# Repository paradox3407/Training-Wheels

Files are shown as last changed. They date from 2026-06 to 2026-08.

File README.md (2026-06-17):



# Training Wheels

ESP32 based two wheeled self balancing robot with a custom PCB, chassis, firmware! Want to learn how to implement a control loop or just want to build a cool robot? Training Wheels is for you! 

## Features

- PID Control Algorithm 
- IMU Calibration Program
- Convenient Troubleshooting:
  - Headers for swapping ICs: ESP32, MPU6050, A4988 Stepper Motor Driver Breakout
  - LED indicators for VDD and GPIO 
- Nema 17 Stepper Motors
- Power Switch

## Overview

This project was made for [Hackclub's](https://hackclub.com/programs) Fallout Program. I built this because I wanted to make a project that encompasses mechanical, electrical, and software engineering, all while exploring PID control through implementing the prototyping process and good design practices. Through the ~70 hours spent on this project I learned the value of documentation, time management, how to select components, read datasheets, how to CAD using assemblies and designing in context, schematic, part layout and wiring good practices, version control, PID control theory and tuning, and so much more! (Might have gotten a caffeine addiction too...)

## Gallery 

<details>
  <summary> Click to expand </summary>
  <br>

  ### Chassis / Assembly
  *Designed in Onshape* 
  
  Source Files found [here](https://cad.onshape.com/documents/563a6cb8d162cb6cd823a1f9/w/2660c435afac39828b2200f7/e/e81ee193bff4145dfd9a22a6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)

  <p align="center">
    
    
  </p>

  ### PCB 
  *Designed in KiCad*

  <p align="center">
    
  </p>

  #### Schematic
  Schematic

  #### Layout
  PCB Layout

</details>

## Firmware (Setup + Tuning)

*Written in C++ using VSCode + [PlatformIO](https://platformio.org/)*

### How to Build & Flash
1. Clone this repository.
2. Open the `Firmware/Self-Balancing-Robot` folder in VS Code with PlatformIO installed.
3. Connect your ESP32 via USB.
4. Click the PlatformIO **Upload** button 

The IMU must be calibrated before running the main code. Run the [calibration program](./Firmware/Self-Balancing-Robot/src/calibration/MPU_calibration.cpp) while the robot is upright and in a stable position. 

### How to Tune

Then run the [main code](./Firmware/Self-Balancing-Robot/src/robot_main/main.cpp). To get the robot to balance, modify these values:

```cpp
const float desiredOutput = 0; // desired angle 
const float Kp = 0; 
const float Ki = 0;
const float Kd = 0; 
```
Tune these values in the following order: 
`desiredOutput` is used for setting the offset for the balance point of the robot. 

`Kp` is the proportional gain, and it will be doing most of the "work": increase by powers of two until the robot oscillates, then decrease by 20%.

`Kd` is the derivative gain, and it addresses oscillations. Increase by small increments, starting roughly at 0.05, until the robot stops oscillating. 

`Ki` is the integral gain, which address drift. By this point the robot should be balancing but if it glides forward or backwards, increase this value, also starting small. Note that `Ki` might not always need to be modified. 

The key to tuning is patience! Only modify one value at a time, and increment in small values. 

## Zine

*Designed in Figma*

Training Wheels Zine-Final-1

## Acknowledgements

Designed by Sara C / paradox3407

**Special thanks** to my robotics mentors for reviewing my designs and giving me much needed feedback! + Jennifer for creating inspiration/reference sketches for the chassis + Ellie for teaching me the basics of calculus at flex when I was trying to learn the math behind PID + Hackclub and Fallout!

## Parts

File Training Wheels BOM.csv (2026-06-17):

Item | Description | Quantity | Unit Price ($) | Total Price ($) | URL | Running Total ($ with Tax)
Pololu_Breakout_A4988 | Motor Driver | 2 | 8.95 | 17.9 | https://www.pololu.com/product/1182 | 19.2
ECA1HM101 | Capacitor | 2 | $0.45 | $0.90 | https://www.digikey.com/en/products/detail/panasonic-industry/ECA-1HM101/245041 | $20.75
Red SMD LED | Indicator LEDs | 2 | $0.15 | $0.30 | https://www.sparkfun.com/red-led-surface-mount-1206.html | $21.27
Screw_Terminal_01x02 | Power Terminal | 1 | $1.54 | $1.54 | https://www.mouser.com/ProductDetail/Altech/MV-152?qs=sGAEpiMZZMvPvGwLNS6715fLxDSS7ZPWguTwbRPpKV4%3D | $23.93
Wire Ferrules | For Power wires | 1 | 13.18 | 13.18 | https://www.aliexpress.com/i/2251832854626098.html?gatewayAdapt=4itemAdapt | $46.67
Stepper_Motor_bipolar | Motors | 2 | $9.13 | $18.26 | https://www.omc-stepperonline.com/nema-17-bipolar-45ncm-63-74oz-in-1-5a-42x42x39mm-4-wires-w-1m-pin-connector-17hs15-1504s-x1 | $55.43
GY-521 | MPU Breakout Board | 1 | $5.94 | $5.94 | https://www.aliexpress.us/item/3256809115197759.html?src=google&gatewayAdapt=glo2usa | $65.68
620 Ohm Resistor | Resistor | 1 | 0.1 | 0.1 | https://www.mouser.com/ProductDetail/YAGEO/AC1206FR-7W620RL | $65.85
270 Ohm Resistor | Resistor | 1 | $0.19 | $0.19 | https://www.mouser.com/ProductDetail/Vishay/RCA1206270RJNEA?qs=sGAEpiMZZMtlubZbdhIBIOxU6kuYwPD0YBDy2BQIpik%3D | $66.18
DEVKIT_V1_ESP32-WROOM-32 TYPE-C 30PIN | Microcontroller | 1 | $12.24 | $12.24 | https://www.aliexpress.us/item/3256809051361454.html?src=google&gatewayAdapt=glo2usa | $87.29
TSR_1-2450 | DC DC CONVERTER 5V 5W | 1 | $6.16 | $6.16 | https://www.digikey.com/en/products/detail/traco-power/TSR-1-2450/9383780 | $97.92
Bismuth Solder Paste | For SMD Soldering | 1 | 16.99 | 16.99 | https://www.amazon.com/Solder-Paste-Soldering-Electronic-Remove/dp/B0BVKB9PY4 | $127.23
LED Rocker Swith | Power Switch | 1 | $5.73 | $5.73 | https://www.aliexpress.us/item/3256810220221486.html?curPageLogUid=jQC0xfIuNxaA | $137.11
18650 2500mAh 20A Battery | Battery | 3 | $4.99 | $14.97 | https://www.18650batterystore.com/products/samsung-25r-18650?adgroupid=43081474946 | $162.93
18650 Battery Holder | Battery Holder | 1 | $2.40 | $2.40 | https://www.digikey.com/en/products/detail/dfrobot/FIT0539/8549502 | $167.07
S4B-EH | Motor connector | 2 | $0.16 | $0.32 | https://www.digikey.com/en/products/detail/jst-sales-america-inc/S4B-EH/926535 | $167.62
2.54mm 0.1" 15-pin Female Header | ESP32 Header | 2 | $1.63 | $3.26 | https://www.electromaker.io/shop/product/254mm-01-15-pin-female-header | $173.24
WR-PHD 2.54 MM SOCKET HEADER; 8 | Motor Driver Header | 5 | $0.40 | $2.00 | https://www.digikey.com/en/products/detail/w-rth-elektronik/61300811821/17737805 | $176.69
M3-0.5x12 Class 12.9 Alloy Flat Socket Head Cap Screws | Battery Mounting Screws | 6 | 0.18 | 1.08 | https://boltsandnuts.com/products/m3-0-5x12-class-12-9-alloy-flat-socket-head-cap-screws-black-oxide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 | $178.55
M3 x 6mm Full Thread Socket Cap Head Screws | PCB mounting Screws | 11 | 0.26 | 2.86 | https://accu-components.com/us/metric-cap-head-screws/3817-SSCF-M3-6-A2 | $183.48
85mm Mecanum Wheel High Grip Rubber Tires | Wheel | 2 | 6.73 | 13.46 | https://www.aliexpress.us/item/3256804851566721.html?gatewayAdapt=glo2usa4itemAdapt | $206.70
6mm coupling | Wheel Coupling | 2 | 6.73 | 13.46 | https://www.aliexpress.us/item/3256804851566721.html?gatewayAdapt=glo2usa4itemAdapt | $229.92
PCB | PCB | 1 | $4.00 | $4.00 | https://cart.jlcpcb.com/quote | $236.82
 |  |  |  |  | Total: | $236.82

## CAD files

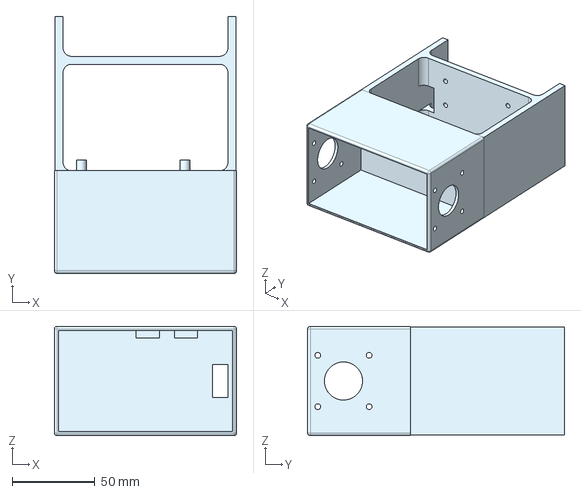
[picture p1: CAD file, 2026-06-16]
CAD Files/3D prints/Chassis V3 - Bottom.step
110.0 x 155.0 x 66.0 mm

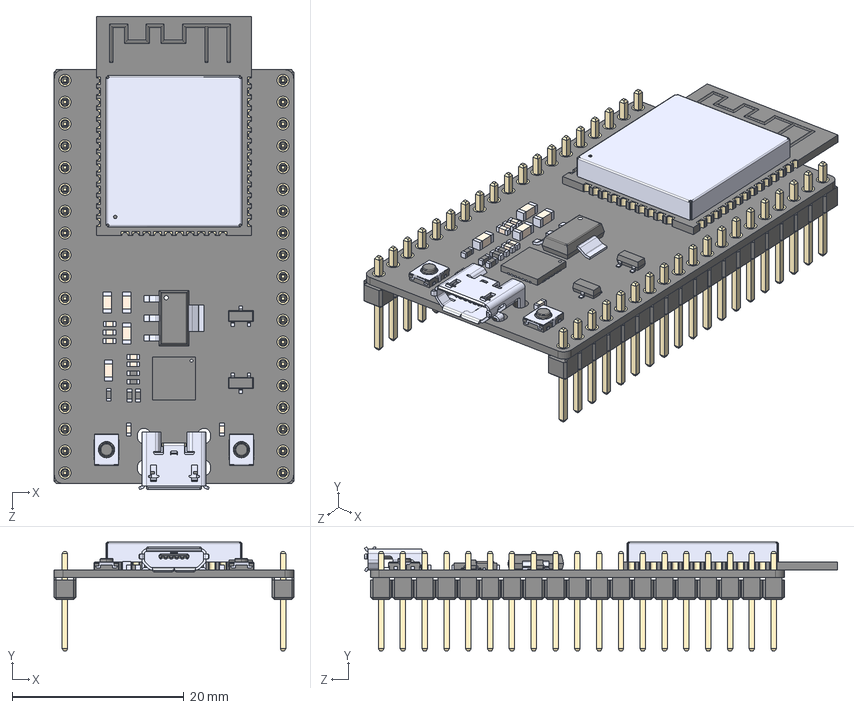
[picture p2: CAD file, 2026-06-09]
CAD Files/PCB Design/Kicad Tools/DEVKIT_V1_ESP32-WROOM-32/DEVKIT_V1_ESP32-WROOM-32.step
27.9 x 12.7 x 55.1 mm
board
header x 2
ESP32-WROOM-32D
micro usb
button x 2
CP2102N-A01-GQFN28
AMS1117-3.3
SS8050-G
components^DEVKIT V1 ESP32-WROOM-32

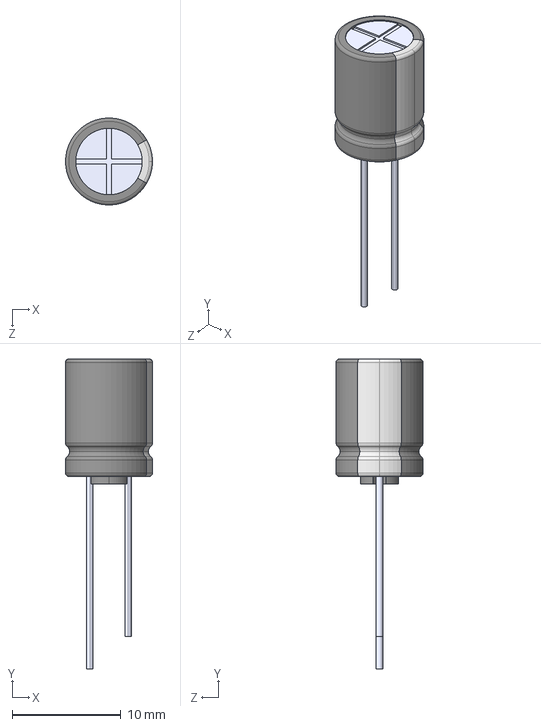
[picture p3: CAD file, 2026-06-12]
CAD Files/PCB Design/Kicad Tools/ECA1HM101/ECA1HM101.step
8.00 x 28.5 x 7.99 mm

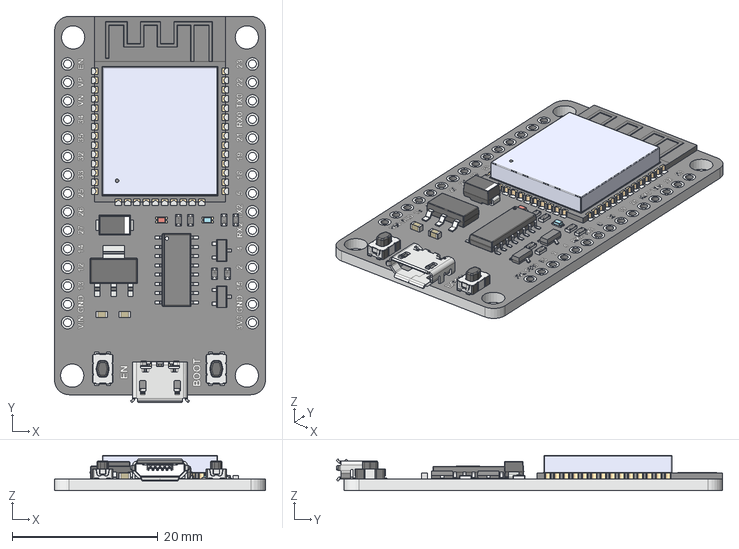
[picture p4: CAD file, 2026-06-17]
CAD Files/PCB Design/Kicad Tools/esp32_30pin-v3.step
29.0 x 53.1 x 4.86 mm

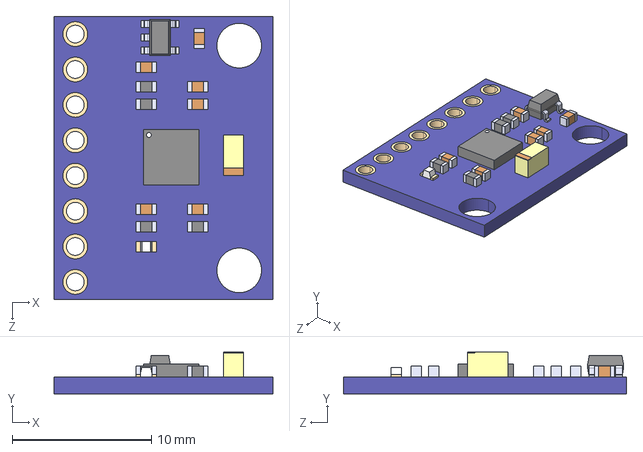
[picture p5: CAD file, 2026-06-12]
CAD Files/PCB Design/Kicad Tools/GY-521/GY-521.step
15.7 x 3.00 x 20.3 mm

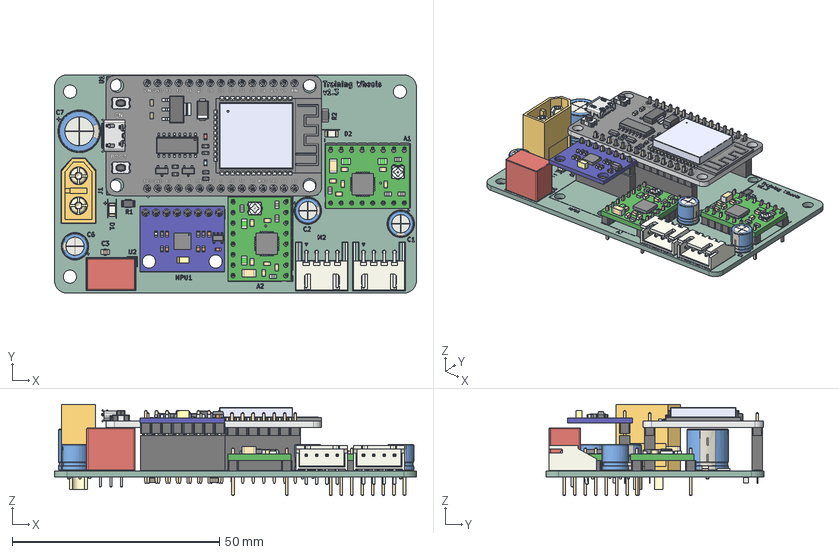
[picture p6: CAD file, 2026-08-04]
CAD Files/PCB Design/Self Balancing Robot/Self Balancing Robot.step
87.4 x 52.7 x 22.0 mm
R_1206_3216Metric x 2
CP_Radial_D6.3mm_P2.50mm x 3
GY-521
PinHeader_1x08_P2.54mm_Vertical x 5
PinSocket_1x08_P2.54mm_Vertical
MICRO USB B
PinSocket_1x15_P2.54mm_Vertical x 2
PinHeader_1x15_P2.54mm_Vertical x 2
JST_XH_S4B-XH-A_1x04_P2.50mm_Horizontal x 2
Converter_DCDC_TRACO_TSR-1_THT
CP_Radial_D10.0mm_P5.00mm
AMASS_XT60-M_1x02_P7.2mm_Vertical
a4988-stepper-motor-driver-carrier x 2
LED_1206_3216Metric x 2
C_0805_2012Metric x 3
Self Balancing Robot_silkscreen x 2
Self Balancing Robot_PCB

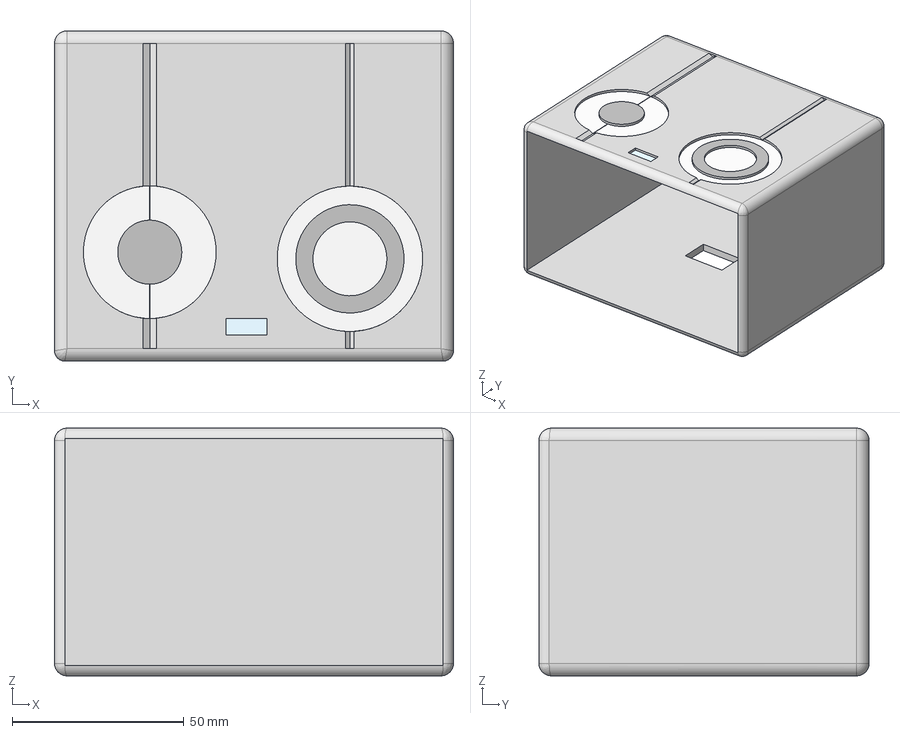
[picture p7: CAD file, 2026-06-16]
CAD Files/3D prints/Chassis V3 - Top.step
116.0 x 96.0 x 72.0 mm

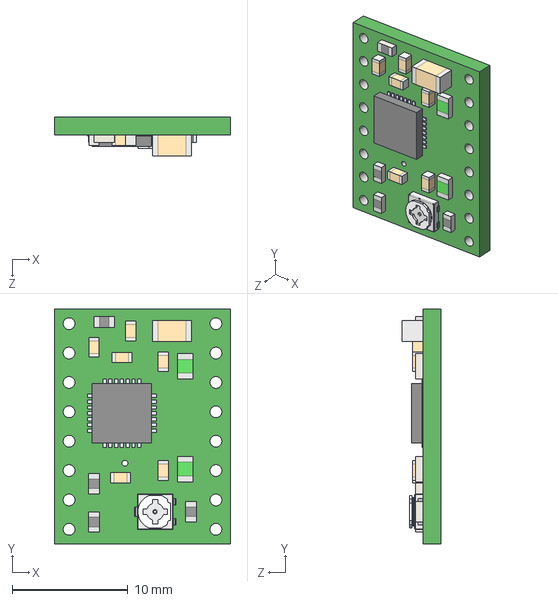
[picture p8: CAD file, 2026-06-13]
CAD Files/PCB Design/Kicad Tools/a4988-stepper-motor-driver-carrier.step
15.2 x 20.3 x 3.37 mm

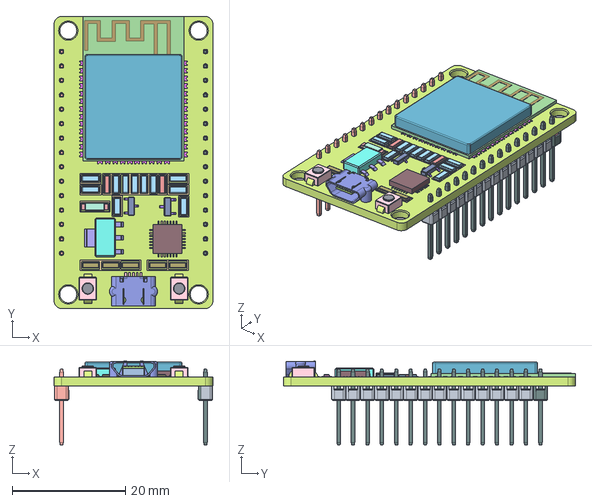
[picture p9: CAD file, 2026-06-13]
CAD Files/PCB Design/Kicad Tools/ESP32 dev Kit v1.step
28.0 x 51.5 x 14.8 mm

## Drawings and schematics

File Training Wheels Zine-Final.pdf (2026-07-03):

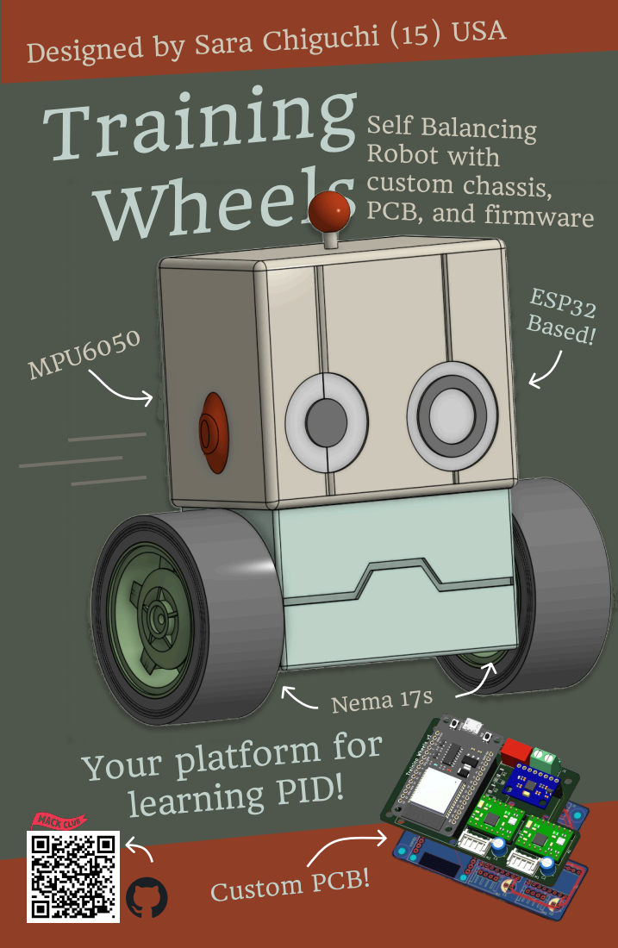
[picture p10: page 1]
Training; Wheels; Self Balancing; Robot with; custom chassis,; MPU6050; learning PID!; Nema 17s; Custom PCB!; ESP32 Based!

Designed by Sara Chiguchi (15) USA

PCB, and firmware

Your platform for

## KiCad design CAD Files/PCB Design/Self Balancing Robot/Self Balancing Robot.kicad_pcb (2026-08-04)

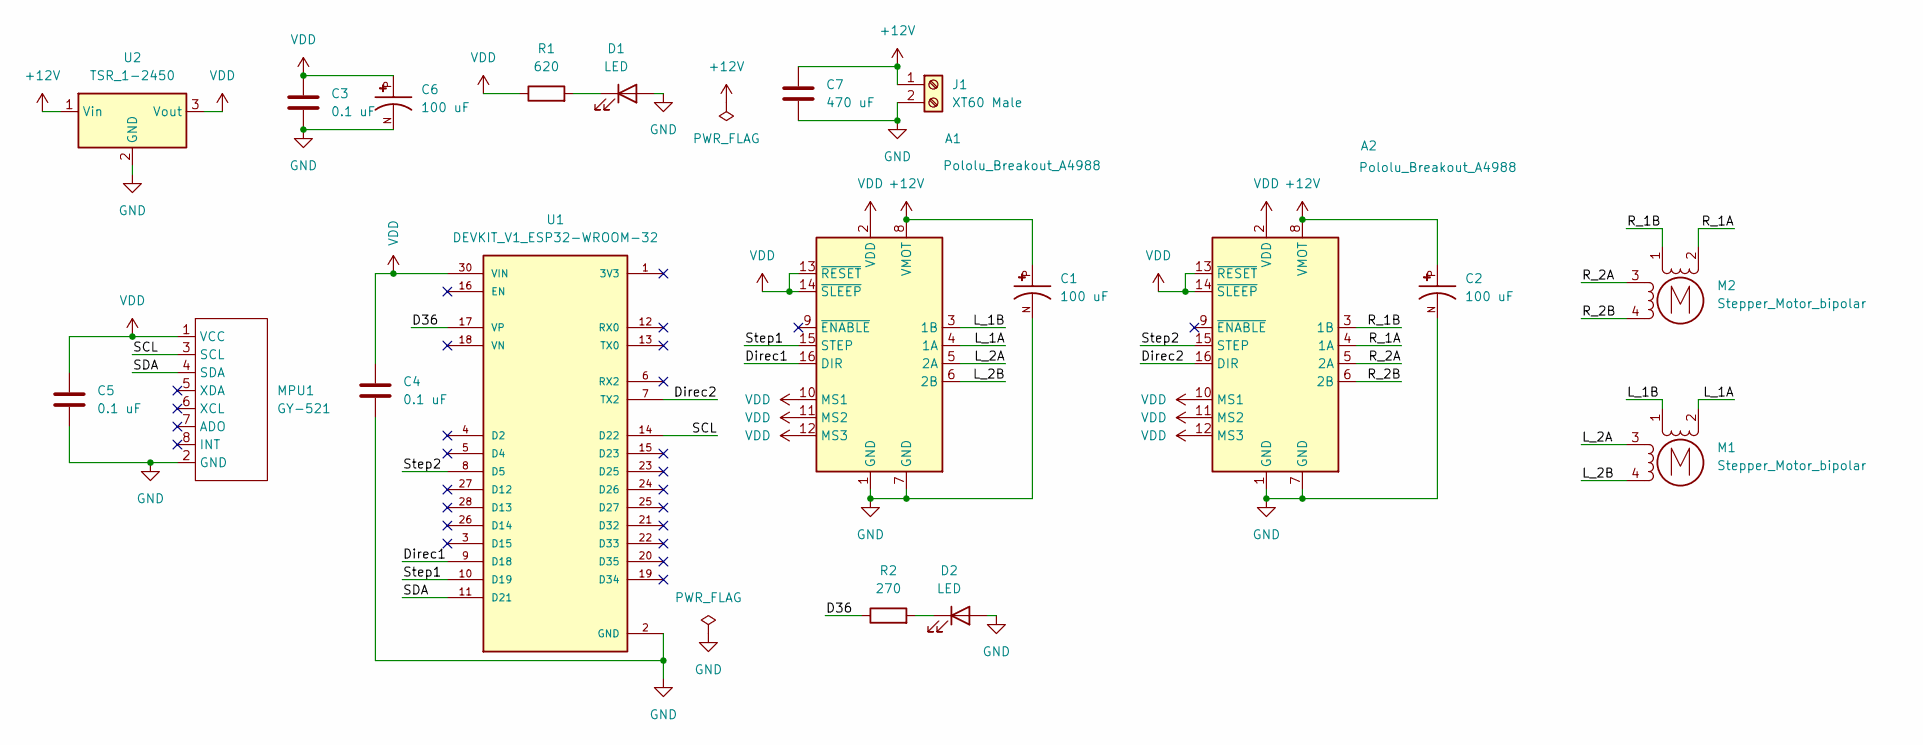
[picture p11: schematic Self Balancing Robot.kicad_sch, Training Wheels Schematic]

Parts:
A1, A2: Pololu_Breakout_A4988; Pololu_Breakout-16_15.2x20.3mm
C1, C2, C6: 100 uF; CP_Radial_D6.3mm_P2.50mm; PARTREV 20-DEC-19
C3, C4, C5: 0.1 uF; C_0805_2012Metric_Pad1.18x1.45mm_HandSolder
C7: 470 uF; CP_Radial_D10.0mm_P5.00mm
D1, D2: LED; SMD LED 1206
J1: XT60 Male; AMASS_XT60-M_1x02_P7.20mm_Vertical
M1, M2: Stepper_Motor_bipolar; JST_XH_S4B-XH-A_1x04_P2.50mm_Horizontal
MPU1: GY-521; MODULE_GY-521
R1: 620; R_1206_3216Metric_Pad1.30x1.75mm_HandSolder
R2: 270; R_1206_3216Metric_Pad1.30x1.75mm_HandSolder
U1: DEVKIT_V1_ESP32-WROOM-32; MODULE_DEVKIT_V1_ESP32-WROOM-32
U2: TSR_1-2450; Converter_DCDC_TRACO_TSR-1_THT

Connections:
+12V: A1.8 (VMOT), A2.8 (VMOT), C1.P, C2.P, C7.1, J1.1, U2.1 (Vin)
/D36: R2.1, U1.17 (VP)
/Direc1: A1.16 (DIR), U1.9 (D18)
/Direc2: A2.16 (DIR), U1.7 (TX2)
/L_1A: A1.4 (1A), M1.2 (-)
/L_1B: A1.3 (1B), M1.1
/L_2A: A1.5 (2A), M1.3
/L_2B: A1.6 (2B), M1.4
/R_1A: A2.4 (1A), M2.2 (-)
/R_1B: A2.3 (1B), M2.1
/R_2A: A2.5 (2A), M2.3
/R_2B: A2.6 (2B), M2.4
/SCL: MPU1.3 (SCL), U1.14 (D22)
/SDA: MPU1.4 (SDA), U1.11 (D21)
/Step1: A1.15 (STEP), U1.10 (D19)
/Step2: A2.15 (STEP), U1.8 (D5)
GND: A1.1 (GND), A1.7 (GND), A2.1 (GND), A2.7 (GND), C1.N, C2.N, C3.2, C4.2, C5.2, C6.N, C7.2, D1.2 (A), D2.2 (A), J1.2, MPU1.2 (GND), U1.2 (GND), U1.29 (GND), U2.2 (GND)
unnamed: D1.1 (K), R1.2
unnamed: D2.1 (K), R2.2
VDD: A1.2 (VDD), A1.10 (MS1), A1.11 (MS2), A1.12 (MS3), A1.13 (~RESET), A1.14 (~SLEEP), A2.2 (VDD), A2.10 (MS1), A2.11 (MS2), A2.12 (MS3), A2.13 (~RESET), A2.14 (~SLEEP), C3.1, C4.1, C5.1, C6.P, MPU1.1 (VCC), R1.1, U1.30 (VIN), U2.3 (Vout)

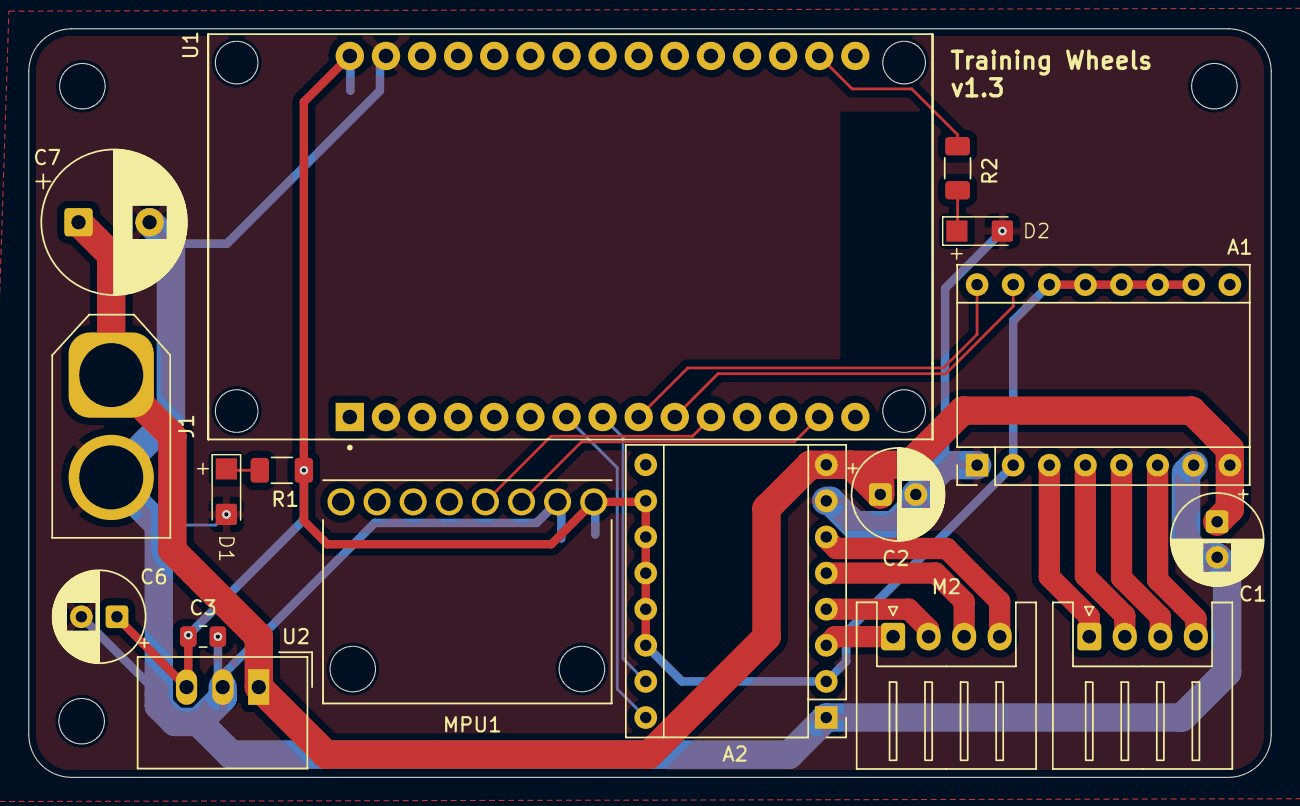
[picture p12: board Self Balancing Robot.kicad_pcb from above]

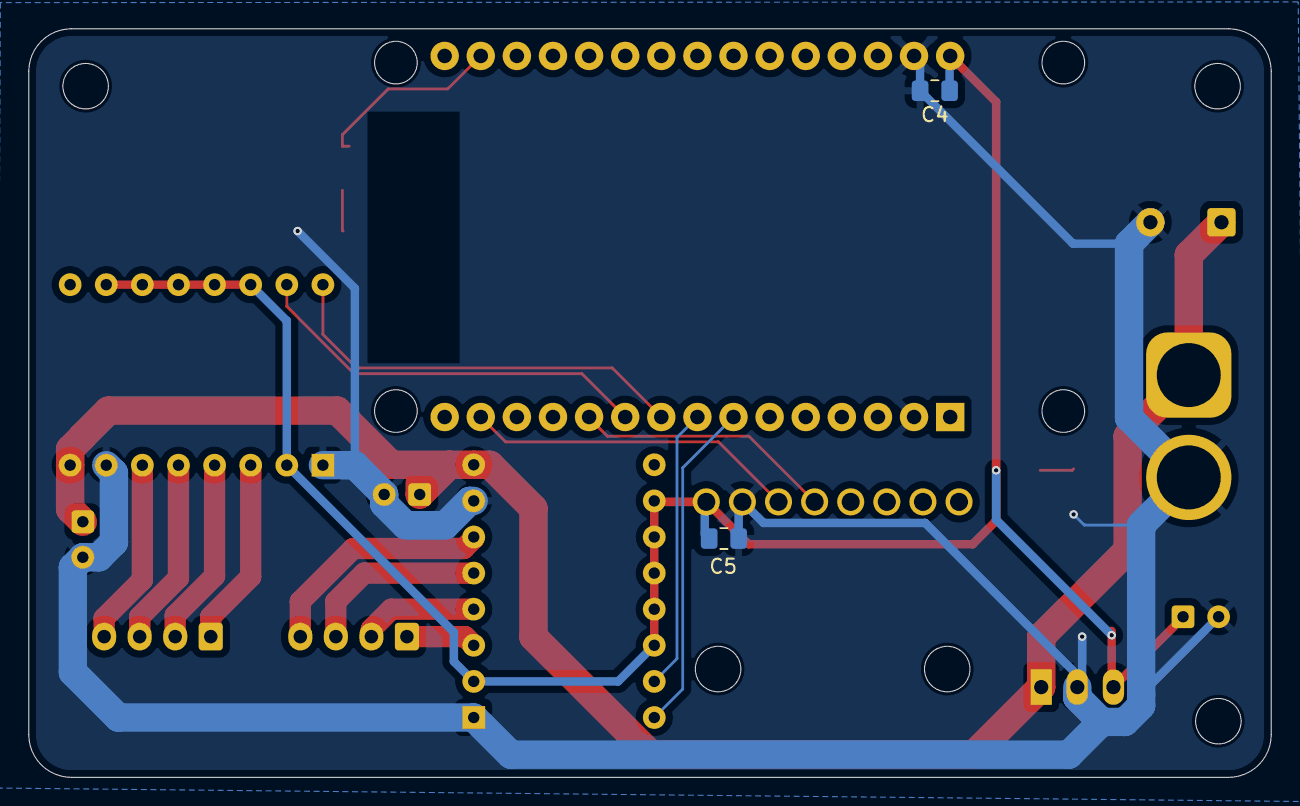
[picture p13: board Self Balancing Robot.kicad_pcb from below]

Board: 2 copper layers, 87.4 x 52.7 mm, 19 parts (2 on the bottom side), 20 nets.

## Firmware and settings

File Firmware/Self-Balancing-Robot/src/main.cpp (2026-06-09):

  // libraries
  #include <MPU6050_light.h>
  #include <Wire.h>

  // global variables
  // declaring pins
  const int pwm1 = 18, int1 = 19, int2 = 21;
  const int pwm2 = 22, int3 = 23, int4 = 25; 
  // MPU I2c pinss
  const int SDA_PIN = 21;
  const int SCL_PIN = 22;

  const float desiredOutput = -1.9; // desired angle (r)
  const float Kp = 80; 
  const float Ki = 120;
  const float Kd = 0.4; 
  const int minSpeed = 0; 
  



  // declare mpu object
  MPU6050 mpu(Wire);


  void setup() {
    // declaring pin modes
    pinMode(pwm1, OUTPUT);
    pinMode(int1, OUTPUT);
    pinMode(int2, OUTPUT);
    pinMode(pwm2, OUTPUT);
    pinMode(int3, OUTPUT);
    pinMode(int4, OUTPUT);

    Serial.begin(115200);             // begin Serial communication
    Wire.begin(SDA_PIN, SCL_PIN);     // explicit I2C pins for ESP32
    Wire.setWireTimeout(3000, true);  // 3ms timeout, reset on timeout
    byte mpuSucess = mpu.begin();     // confused about parameters, return byte
    if (mpuSucess == 0) {
      Serial.println("MPU connected successfully!");
    } else {
      Serial.println("MPU connecton failed.");
      while (1) {  // while true, so delay indefinitly
        delay(10);
      }
    }
    // set mpu offsets
    mpu.setAccOffsets(-0.0743398427, 0.0285234403, -0.0075678706);
    mpu.setGyroOffsets(0.7554199695, 0.7554199695, 0.7554199695);

    // configure PWM channels for ESP32
    ledcSetup(pwmChannel1, pwmFreq, pwmResolution);
    ledcAttachPin(pwm1, pwmChannel1);
    ledcSetup(pwmChannel2, pwmFreq, pwmResolution);
    ledcAttachPin(pwm2, pwmChannel2);
  }

  void setMotors(float u) {
    u = constrain(u, -255, 255);
    if (u < minSpeed && u > 0){
      u = minSpeed; 
    }
    else if (u > -minSpeed && u < 0)
    {
      u = -minSpeed;
    }
    if (u > 0) {
      digitalWrite(int1, HIGH);  
      digitalWrite(int2, LOW);
      digitalWrite(int3, LOW);
      digitalWrite(int4, HIGH);
      ledcWrite(pwmChannel1, (int)constrain(u, 0, 255));
      ledcWrite(pwmChannel2, (int)constrain(u, 0, 255));
    } else {
      digitalWrite(int1, LOW);
      digitalWrite(int2, HIGH);
      digitalWrite(int3, HIGH);
      digitalWrite(int4, LOW);
      ledcWrite(pwmChannel1, (int)constrain(-u, 0, 255));
      ledcWrite(pwmChannel2, (int)constrain(-u, 0, 255));
    }

  }
  void loop() {
    static unsigned long lastTime = 0;
    static float integral = 0;
    static float lastError = 0;
    static int printCounter = 0;

    unsigned long now = micros();
    float dt = (now - lastTime) / 1000000.0;  // seconds
    // enforce ~5ms loop period (200Hz) for consistent timing
    if (dt < 0.005) return;

    lastTime = now;
    mpu.update();                    // update data, returns void
    float angleY = mpu.getAngleY();  // declaring here to minimize scope
    
    if (abs(angleY)>60){
      digitalWrite(int1, LOW);
      digitalWrite(int2, LOW);
      digitalWrite(int3, LOW);
      digitalWrite(int4, LOW);
      while (1) { // while true, so delay indefinitly 
        delay(10); 
      }
      Serial.println("It fell..");
    }
    
    float error = desiredOutput - angleY;

    // P term 
    float P = Kp * error; 

    // I term 
    integral += error * dt;
    integral = constrain(integral, -100, 100);
    float I = Ki * integral;

    // D term 
    float derivative = (error - lastError) / dt;
    float D = Kd * derivative;
    lastError = error;

    float u = P + I + D; 

    setMotors(u);
    if (++printCounter >= 10) {
      Serial.print("Error:");
      Serial.print(error);
      Serial.print(",");
      Serial.print("Integral:");
      Serial.print(I);
      Serial.print(",");
      Serial.print("AngleY:");
      Serial.print(angleY);
      Serial.print(",");
      Serial.print("u:");
      Serial.println(constrain(u, -255, 255));
      printCounter = 0;
    }
    delay(1);
  }

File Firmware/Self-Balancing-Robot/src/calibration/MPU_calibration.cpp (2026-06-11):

// include libraries
#include <Arduino.h>
#include <Wire.h>
#include <MPU6050_light.h>

MPU6050 mpu(Wire);

void setup() {
  Serial.begin(115200);
  Wire.begin();
  byte mpuSucess = mpu.begin();
  if (mpuSucess == 0){
    Serial.println("MPU connected successfully!");
  }
  else {
    Serial.println("MPU connecton failed.");
    while (1) { // while true, so delay indefinitly 
      delay(10); 
    }
  }
  mpu.calcOffsets(true, true);
  float accXoffset = mpu.getAccXoffset(); 
  float accYoffset = mpu.getAccYoffset(); 
  float accZoffset = mpu.getAccZoffset(); 
  float gyroXoffset = mpu.getGyroXoffset();
  float gyroYoffset = mpu.getGyroYoffset();
  float gyroZoffset = mpu.getGyroZoffset();
  Serial.print("accXoffset: ");
  Serial.println(accXoffset, 10);
  Serial.print("accYoffset: ");
  Serial.println(accYoffset, 10);
  Serial.print("accZoffset: ");
  Serial.println(accZoffset, 10);
  Serial.print("gyroXoffset: ");
  Serial.println(gyroXoffset, 10);
  Serial.print("gyroYoffset: ");
  Serial.println(gyroYoffset, 10);
  Serial.print("gyroZoffset: ");
  Serial.println(gyroZoffset, 10);
}
void loop() {
  
}

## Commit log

2026-06-09 Initial commit: Fresh start
    [Chassis V3.obj, DEVKIT_V1_ESP32-WROOM-32.step, Self Balancing Robot.kicad_pcb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]
2026-06-09 Started porting main code (Arduino nano to ESP32)
2026-06-10 Added MPU calibration program
2026-06-11 Ported code to stepper motors and ESP32
2026-06-11 Fix incorrect gyro offset print statements in MPU calibration
    [MPU_calibration.cpp]
2026-06-11 Created PCB schematic
    [Self Balancing Robot.kicad_sch]
2026-06-11 Resolved pin errors
    [Self Balancing Robot.kicad_sch]
2026-06-11 VDD power flag fix
    [Self Balancing Robot.kicad_sch]
2026-06-11 Added battery terminal, updated capacitor symbol, and assigned footprints.
    [Self Balancing Robot.kicad_sch]
2026-06-12 Fix schematic by adding screw terminal for battery, added indicator LEDS (and resistors), made custom footprints for capacitors, LEDS, configured libraries, made gitignore for PCB design folder
    [DEVKIT_V1_ESP32-WROOM-32.step, ECA1HM101.step, Self Balancing Robot.kicad_pcb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]
2026-06-12 Added MPU (GY-521) footprint
    [GY-521.step, Self Balancing Robot.kicad_pcb, Self Balancing Robot.kicad_sch]
2026-06-13 Positioned components on PCB, drew traces, assigned step files
    [ESP32 dev Kit v1.step, Self Balancing Robot.kicad_sch, a4988-stepper-motor-driver-carrier.step]
2026-06-13 Add 3d models
    [Self Balancing Robot.kicad_pcb]
2026-06-14 Fixed minor labeling and wiring aesthetics
    [Self Balancing Robot.kicad_sch]
2026-06-14 Generated gerber files
    [Self Balancing Robot-B_Cu.gbr, Self Balancing Robot-B_Mask.gbr, Self Balancing Robot-B_Paste.gbr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]
2026-06-14 Update .gitignore to exclude additional KiCAD temporary files
    [Self Balancing Robot.kicad_pcb]
2026-06-16 Add CAD settings for Chassis V2 zip file to .gitignore
2026-06-16 Add Bill of Materials (BOM)
    [Training Wheels BOM.csv]
2026-06-16 Add step files
    [Chassis V3 - Bottom.step, Chassis V3 - Top.step, Chassis V3.obj]
2026-06-16 Stop tracking Chassis v2 zip file
2026-06-17 Update Bill of Materials (BOM) with new components and remove obsolete entries
    [Training Wheels BOM.csv]
2026-06-17 Update 3d models of ESP32
    [Self Balancing Robot.kicad_pcb, Self Balancing Robot.step, esp32_30pin-v3.step]
2026-06-17 Add drill files
    [Self Balancing Robot-B_Cu.gbl, Self Balancing Robot-B_Mask.gbs, Self Balancing Robot-B_Paste.gbp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]
2026-06-17 Update with fixed PCB photo
2026-06-17 update with correct Chassis source file
